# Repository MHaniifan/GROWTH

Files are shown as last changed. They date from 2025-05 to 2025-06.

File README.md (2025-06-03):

## GROWTH: Greenhouse Remote Operations With Temperature & Humidity

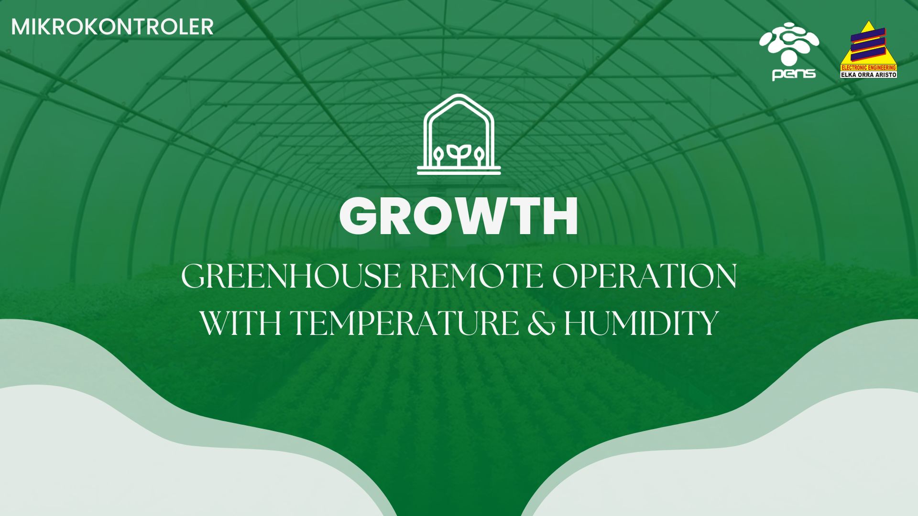
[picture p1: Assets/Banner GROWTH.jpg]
Logo GROWTH


<div align="justify">
    Proyek ini bertujuan untuk mengembangkan sistem automasi cerdas berbasis Mikrokontroler AVR untuk Smart Farming, menggunakan komponen utama seperti Arduino Mega, sensor YL-69 dan DHT-11, serta pompa air dan kipas. Arduino Mega bertindak sebagai mikrokontroler utama yang mengontrol komunikasi antar sensor dan aktuator, memungkinkan pemantauan dan pengontrolan secara real-time. Sistem ini menggunakan Timer pada AVR untuk menjaga sinkronisasi waktu, dan Interrupt untuk menyalakan Pompa Air ketika kelembaban dibawah batas.
</div>

<div align="justify">
    Pompa Air akan menyala setiap jadwal penyiraman yang sudah ditentukan. Dimana jadwal penyiraman dan lama pompa menyala, diatur pada GUI pada Komputer yang terhubung ke Mikrokontroler menggunakan komunikasi UART. Untuk Kipas akan menyala setiap suhu telah melewati batas yang ditentukan, dimana batas suhunya dapat diatur pada GUI.
</div>

<div align="justify">
    Dengan menggunakan UART, seluruh data dari sensor-sensor ini dikirimkan ke Komputer. Memungkinkan petani untuk memantau penggunaan energi dan kondisi lingkungan secara langsung dari Komputer. Sistem ini dirancang untuk meningkatkan efisiensi energi, hasil produksi, serta dapat mengurangi kerugian dengan mengotomatiskan berbagai fungsi dan memberikan kendali yang lebih fleksibel.
</div>

## Supported By :
>- Dosen Pengampu : Akhmad Hendriawan ST., MT. (NIP.197501272002121003)
>- Mata kuliah : Mikrokontroler
>- Program Studi : Sarjana Terapan Teknik Elektronika
>- Politeknik Elektronika Negeri Surabaya<br> 

## Team Member :
| NRP | Nama | Jobdesk | Github |
| :---:|:---:| :---:| :-----:|
| 2123600007 | Muhammad Haniifan  | Project Manager | [Haniifan](https://github.com/MHaniifan)
| 2123600011 | Monalisa Br. Sidauruk | Hardware Specialist | [Lisa](https://github.com/MonalisaSidauruk)
| 2123600015 | Fakhrihans Ardiyanto | UI/UX Designer | [Rihan](https://github.com/FakhrihansArdiyanto)
| 2123600027 | Darda Drestanala | 3D Designer | [Darda](https://github.com/dardadrestanala)
| 2123600029 | Aurora Putri Salsabillah Rofii | PCB Designer | [Aurora](https://github.com/aurorapsr)
| 2124640016 | Arif Ramadhan | Programmer |[Arif](https://github.com/arif-rmdhn)

##
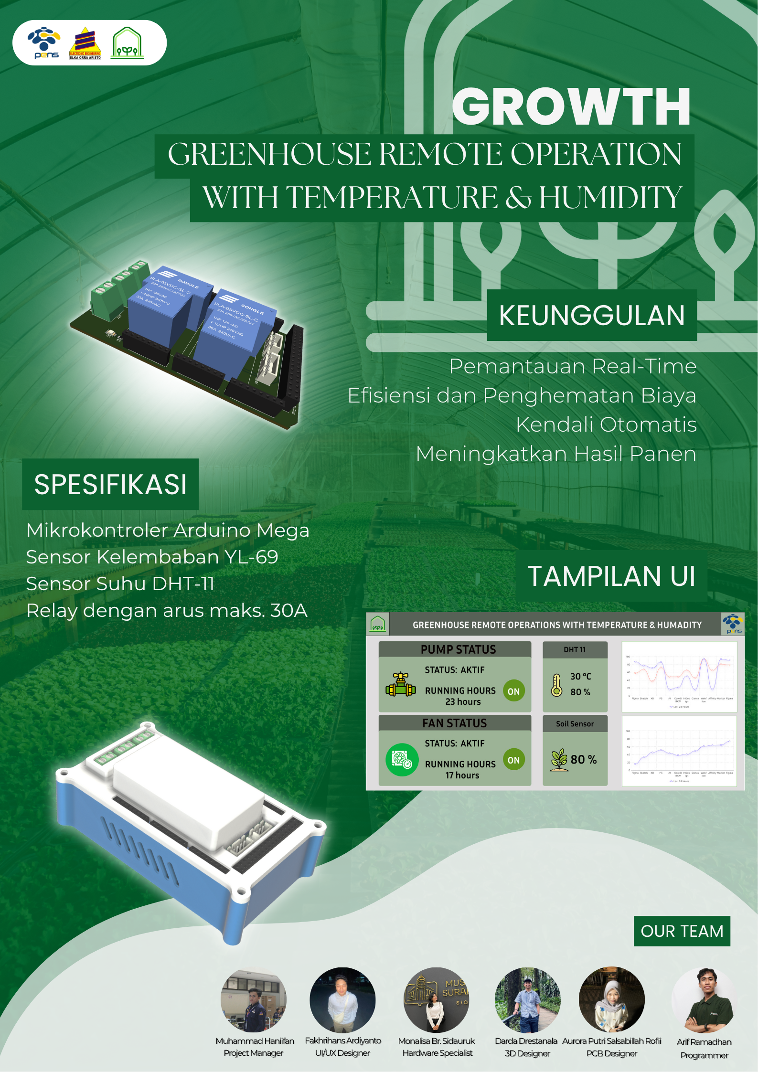
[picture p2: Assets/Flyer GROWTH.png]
Flyer GROWTH


## Daftar Isi
- [Deskripsi Project](https://github.com/MHaniifan/GROWTH#growth-greenhouse-remote-operations-with-temperaturehumidity)
- [Team Member](https://github.com/MHaniifan/GROWTH#team-member-)
- [Keunggulan](https://github.com/MHaniifan/GROWTH#keunggulan)
- [Desain Hardware](https://github.com/MHaniifan/GROWTH#desain-hardware)
- [Printed Circuit Board](https://github.com/MHaniifan/GROWTH#printed-circuit-board-pcb)
- [Program](https://github.com/MHaniifan/GROWTH#program)
- [Tampilan UI/UX](https://github.com/MHaniifan/GROWTH#tampilan-uiux)

## Keunggulan
- **Pemantauan Real-Time**: Mengukur perubahan kelembaban dan suhu dengan sensor secara terus - menerus.
- **Efisiensi dan Penghematan Biaya**: Mengurangi penggunaan listrik karena pompa dan kipas hanya dinyalakan ketika melewati batas normal tanaman.
- **Kendali Otomatis**: Menggunakan sensor untuk mengamati perubahan kondisi dan relay untuk mengaktifkan pompa dan kipas sehingga tidak dikontrol oleh manusia.
- **Meningkatkan Hasil Panen**: Mencegah tanaman kekeringan dan kepanasan sehingga dapat meningkatkan kondisi tanaman.

## Desain Hardware
Blok Diagram
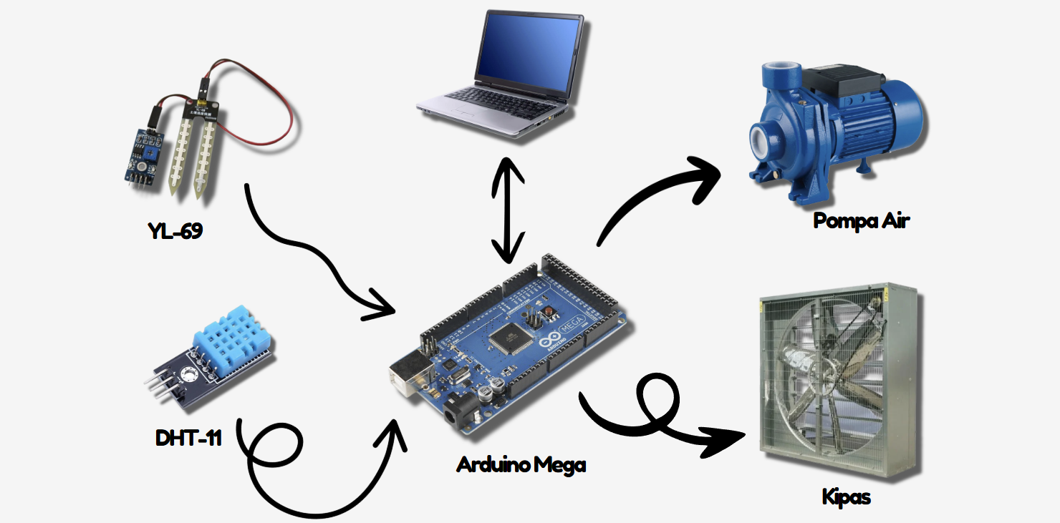
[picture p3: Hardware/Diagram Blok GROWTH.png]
Diagram Blok GROWTH


Wiring Diagram
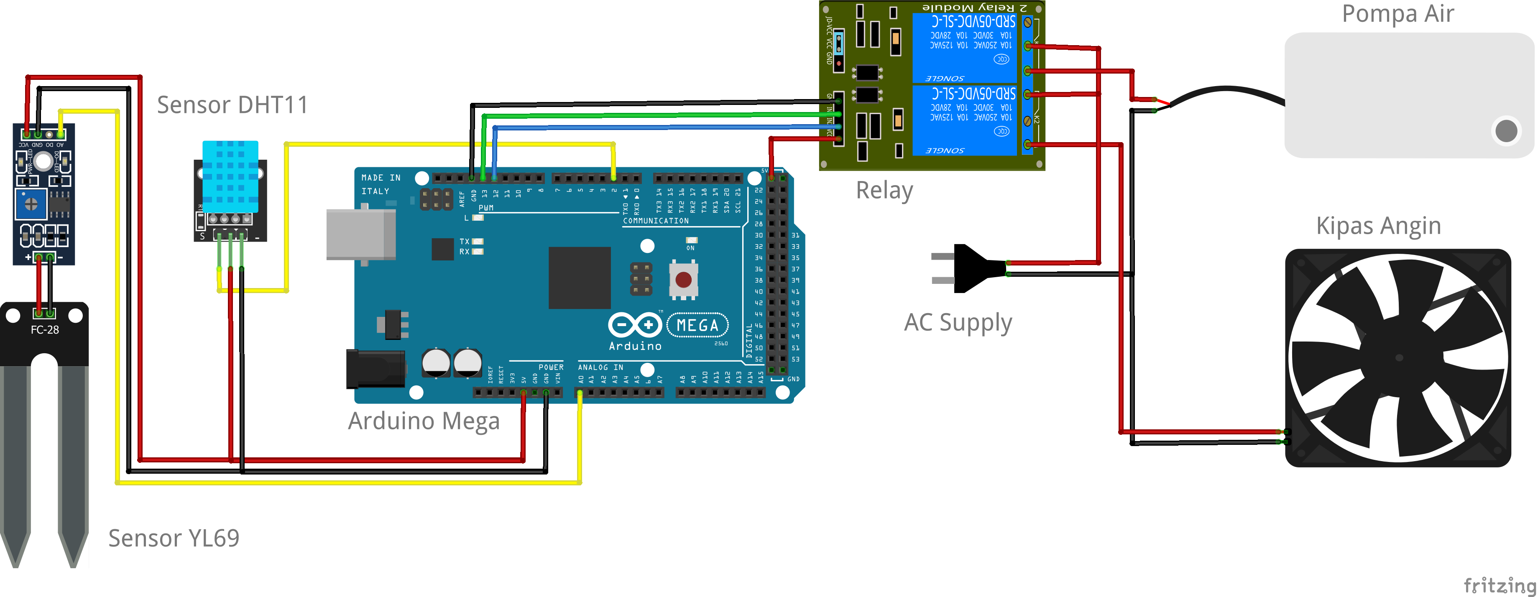
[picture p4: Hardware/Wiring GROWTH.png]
Wiring GROWTH


## Printed Circuit Board (PCB)
Skematik PCB
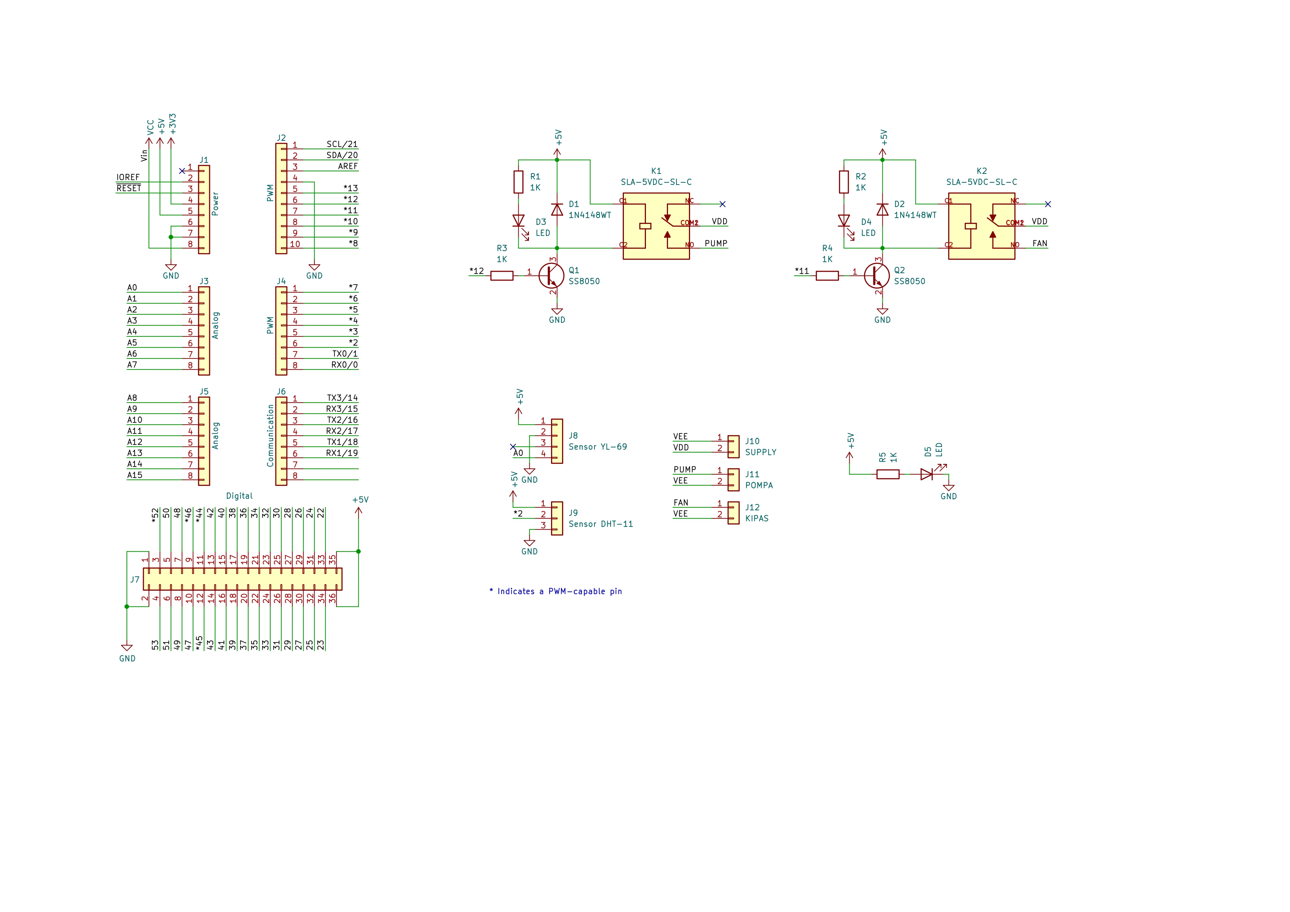
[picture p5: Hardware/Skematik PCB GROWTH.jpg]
Skematik PCB GROWTH


Desain PCB
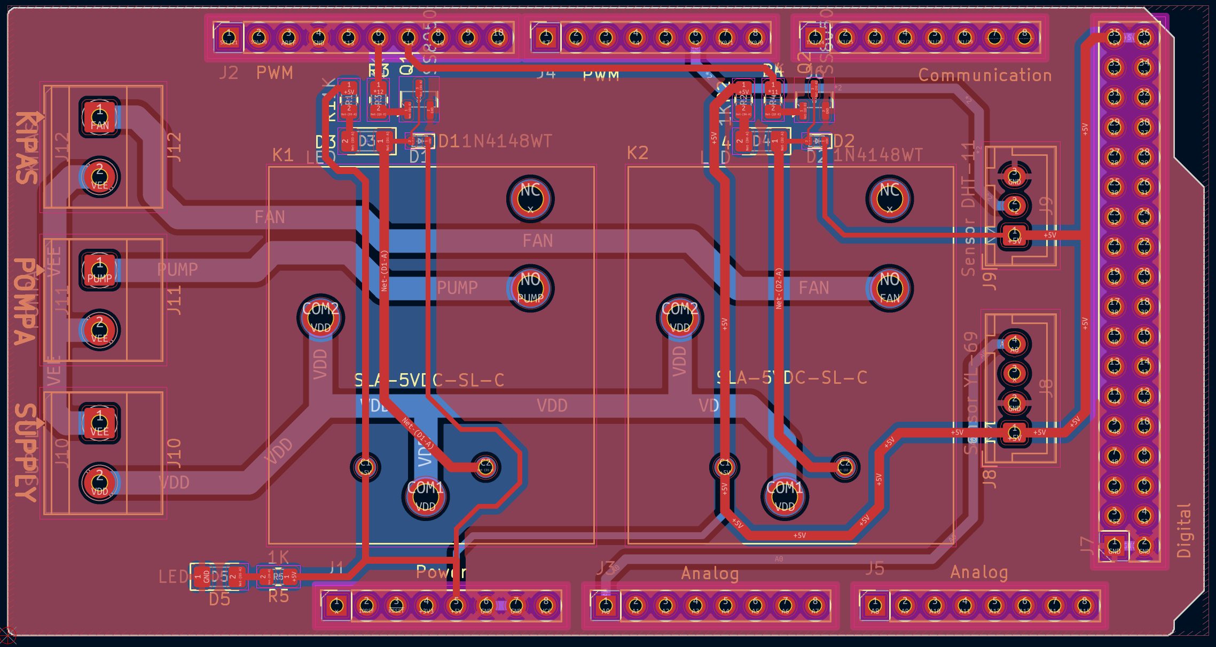
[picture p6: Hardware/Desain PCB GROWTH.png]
Desain PCB GROWTH


## Desain 3D
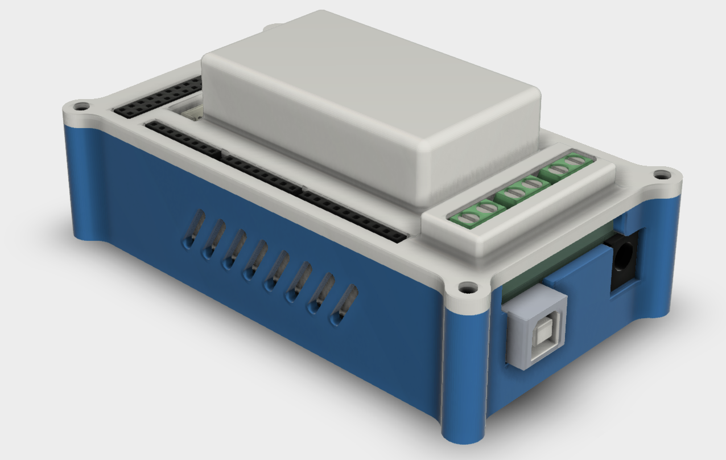
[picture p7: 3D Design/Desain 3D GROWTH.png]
Desain 3D GROWTH


## Flowchart Program
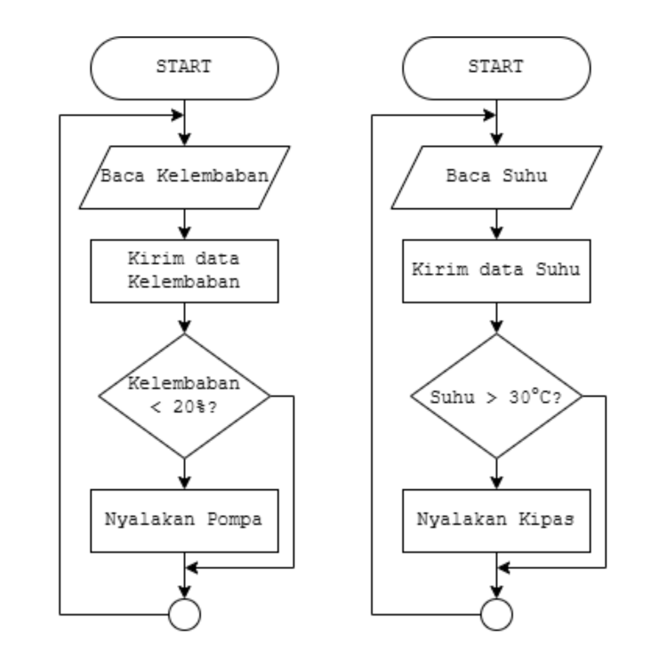
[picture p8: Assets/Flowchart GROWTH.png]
Flowchart GROWTH


## Tampilan UI/UX
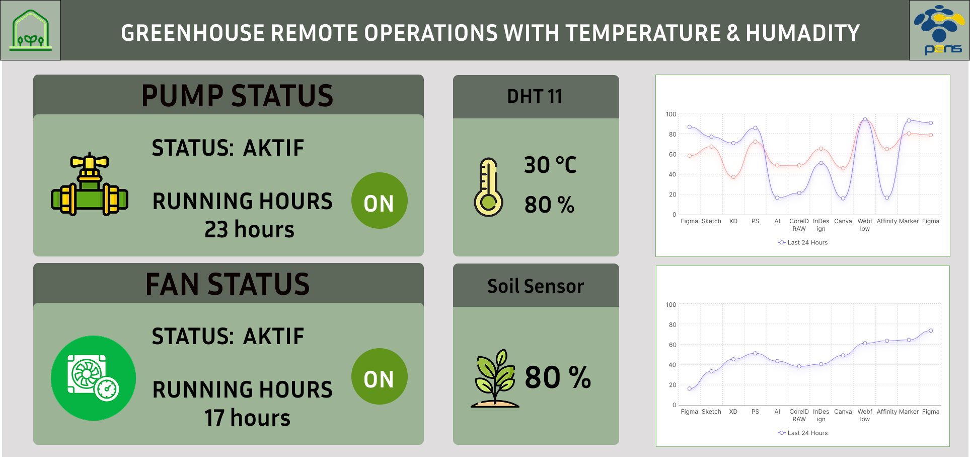
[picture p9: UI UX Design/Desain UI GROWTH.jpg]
Desain UI GROWTH


## Pengembangan Kedepannya
- Penambahan IoT untuk Pemantauan Jarak Jauh
- Penambahan RTC untuk Penjadwalan Penyiraman
- Penambahan Desain Casing yang Tahan Air
- Penambahan Baterai untuk Supply Darurat

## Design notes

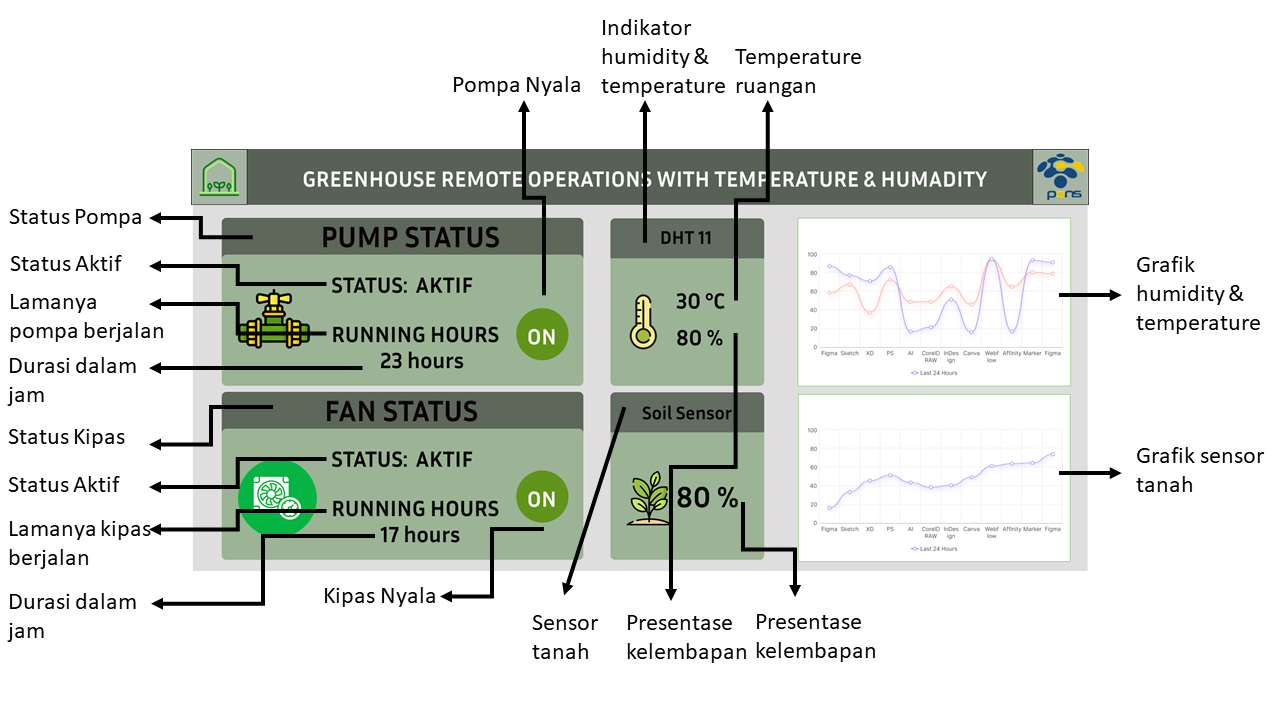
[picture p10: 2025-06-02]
UI UX Design/Deskripsi UI GROWTH.png

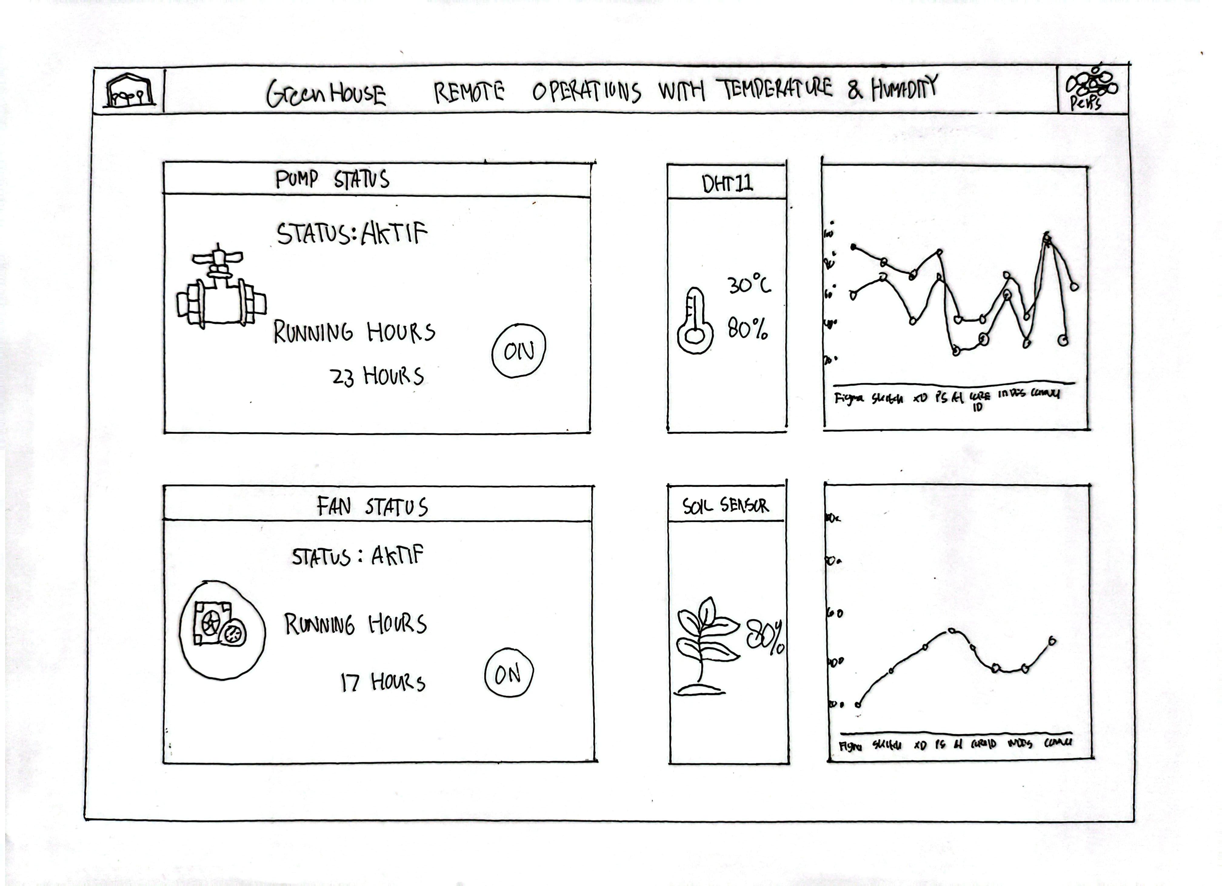
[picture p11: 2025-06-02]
UI UX Design/Sketsa UI GROWTH.jpg

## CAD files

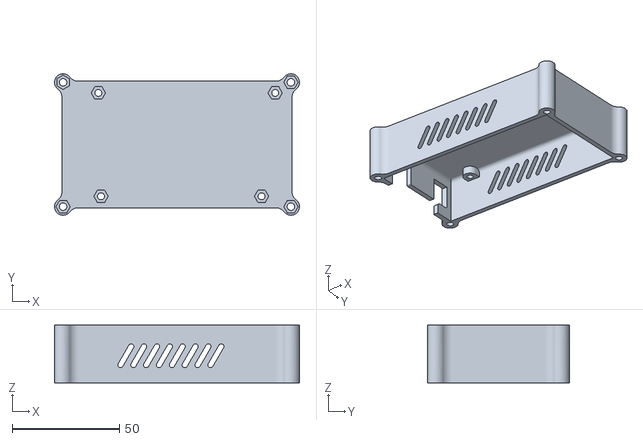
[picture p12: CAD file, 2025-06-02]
3D Design/Case_bottom-Shield.stl
114.3 x 66.0 x 27.0

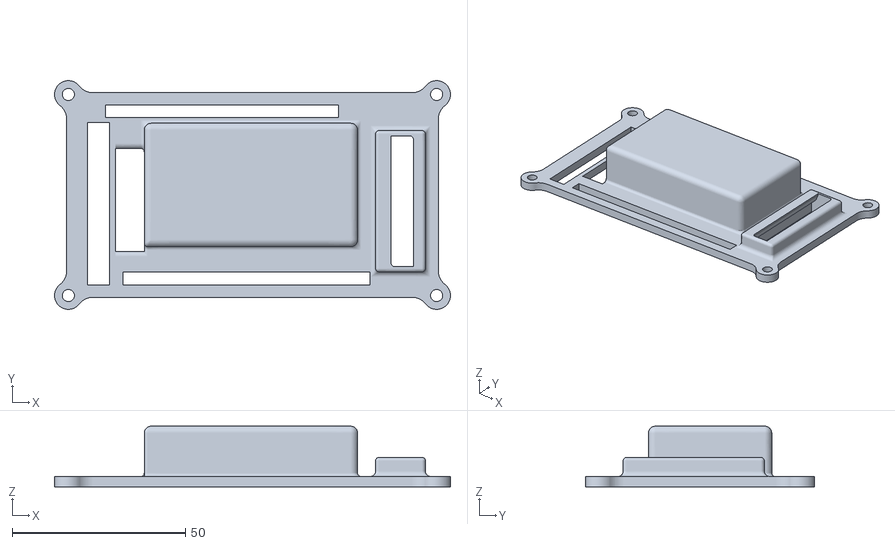
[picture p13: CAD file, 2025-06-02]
3D Design/Case_Top-Shield.stl
114.3 x 66.0 x 17.5

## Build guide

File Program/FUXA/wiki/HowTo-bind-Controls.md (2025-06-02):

To bind a **Output** Control to the Device Tag (Variable): going in editor and select the View.
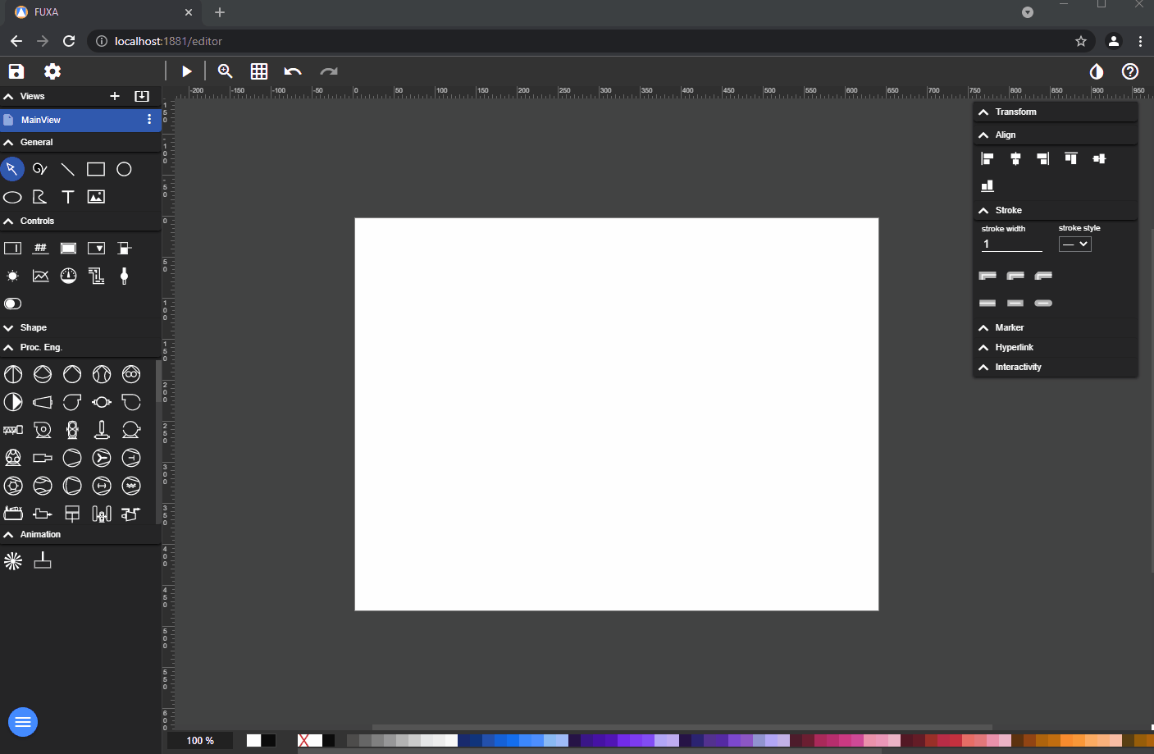
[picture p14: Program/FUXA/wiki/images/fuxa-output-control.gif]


To bind a **Input** Control to Device Tag.
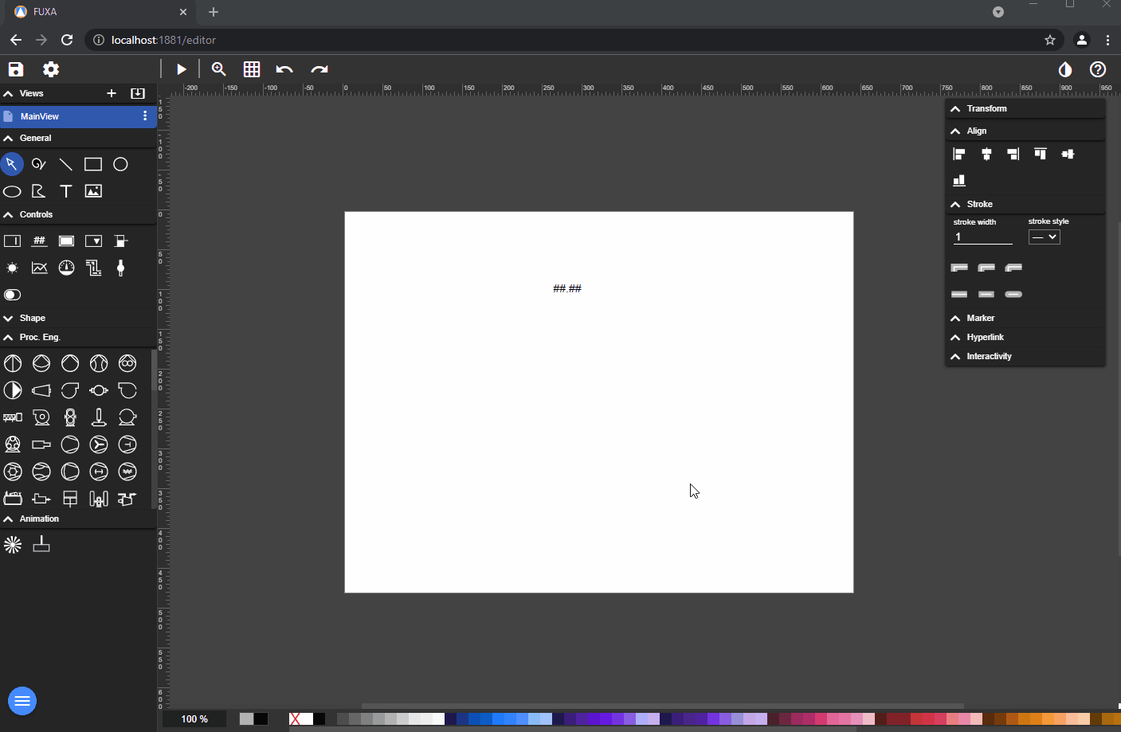
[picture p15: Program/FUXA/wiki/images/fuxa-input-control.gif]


To bind a **Select** Control to Device Tag.
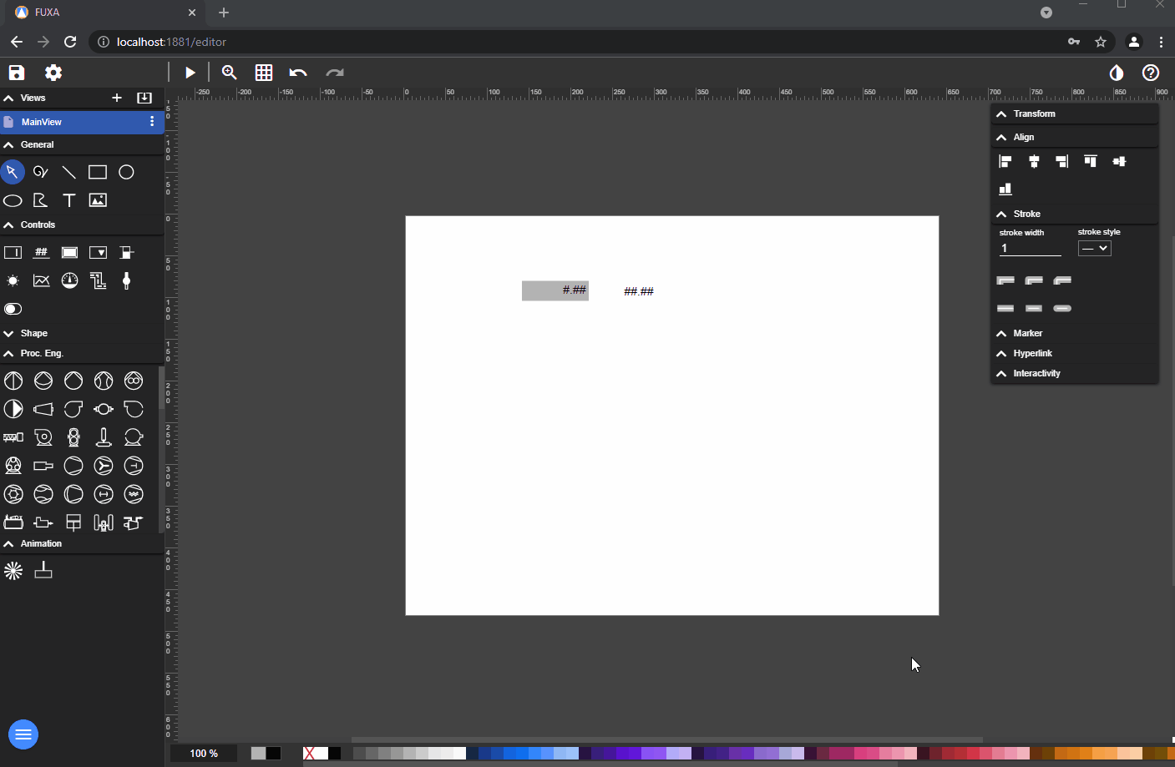
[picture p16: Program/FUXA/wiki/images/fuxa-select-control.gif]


To bind a **Slider** Control to Device Tag.
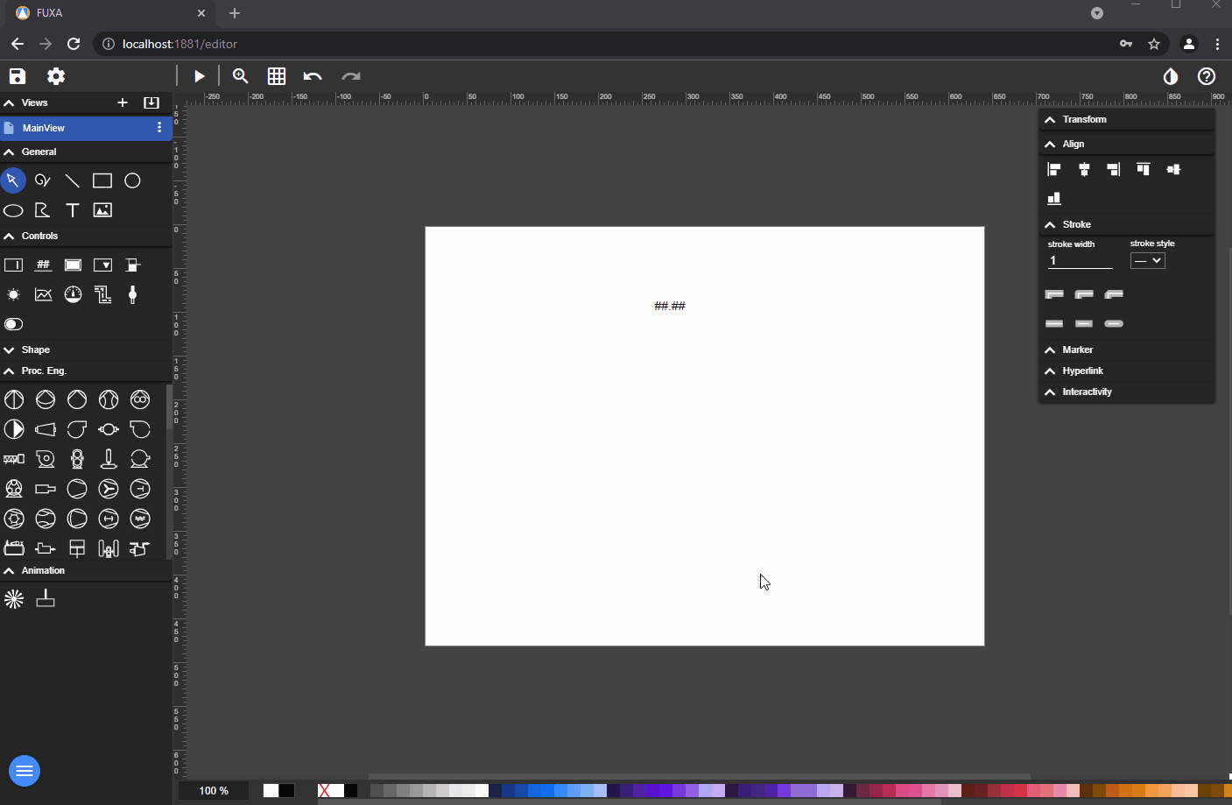
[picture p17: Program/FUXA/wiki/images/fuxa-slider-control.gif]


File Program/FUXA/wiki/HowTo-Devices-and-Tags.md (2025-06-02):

To add your Device and Tags going to **Connections** in editor.

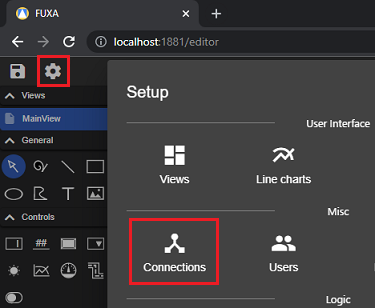
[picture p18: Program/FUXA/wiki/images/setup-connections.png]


Add and connect a **OPCUA** device.
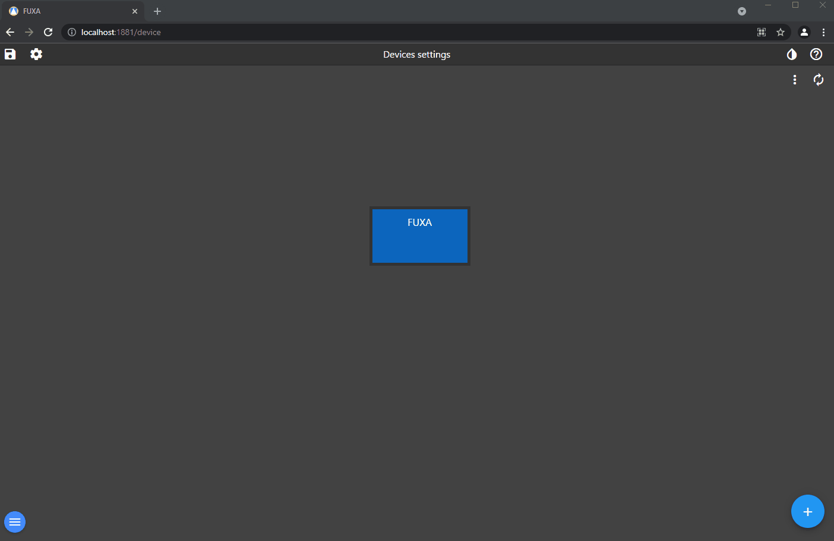
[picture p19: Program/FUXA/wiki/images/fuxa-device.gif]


To add OPCUA Tags the device have to be connected.
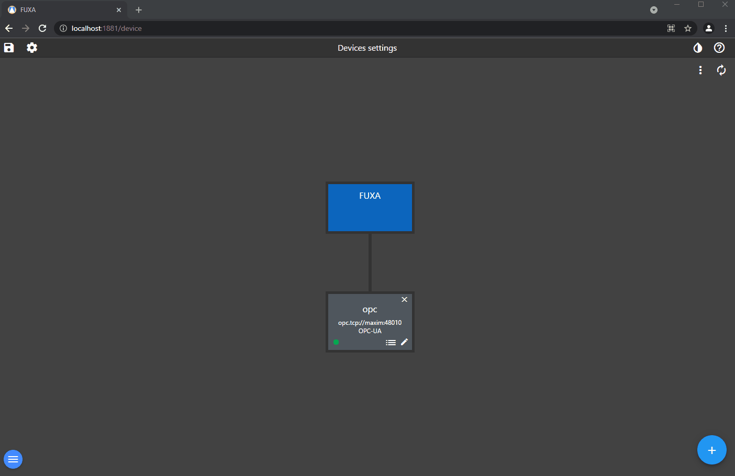
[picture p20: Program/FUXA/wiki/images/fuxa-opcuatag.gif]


To add a **Modbus** connection you have to install the driver in **Plugins**


Add a **MQTT** connection and a topic subscription
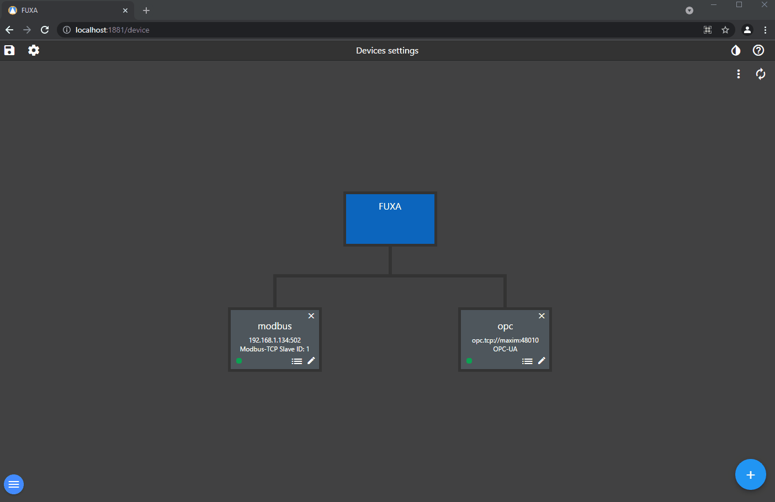
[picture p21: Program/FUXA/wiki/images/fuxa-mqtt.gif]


Add a **WebAPI** connection and a Tag of the JSON result
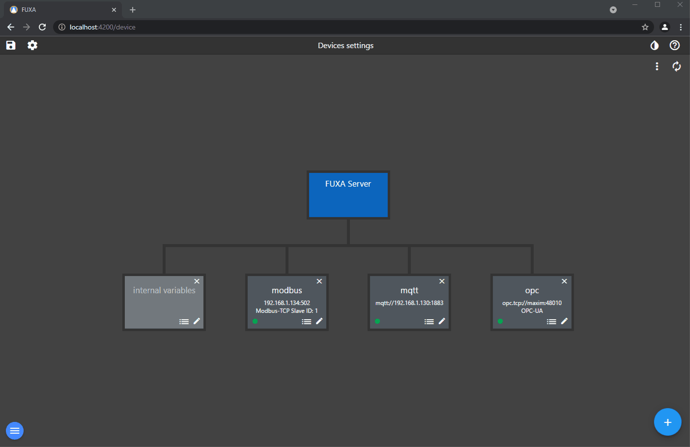
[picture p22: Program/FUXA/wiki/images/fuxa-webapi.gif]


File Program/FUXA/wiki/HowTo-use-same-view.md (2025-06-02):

You can reuse the same **View** for repeating components like pumps and valves.

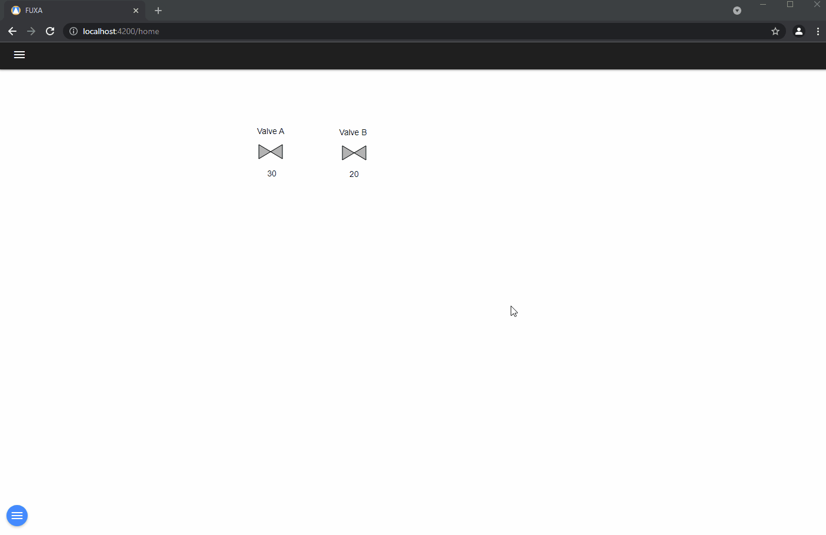
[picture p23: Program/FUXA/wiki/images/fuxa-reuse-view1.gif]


You have to define a device as **internal** and some variable (Tag) and bind it to the controls of reusable **View**.
For example the title dialog and a variable for the input value.

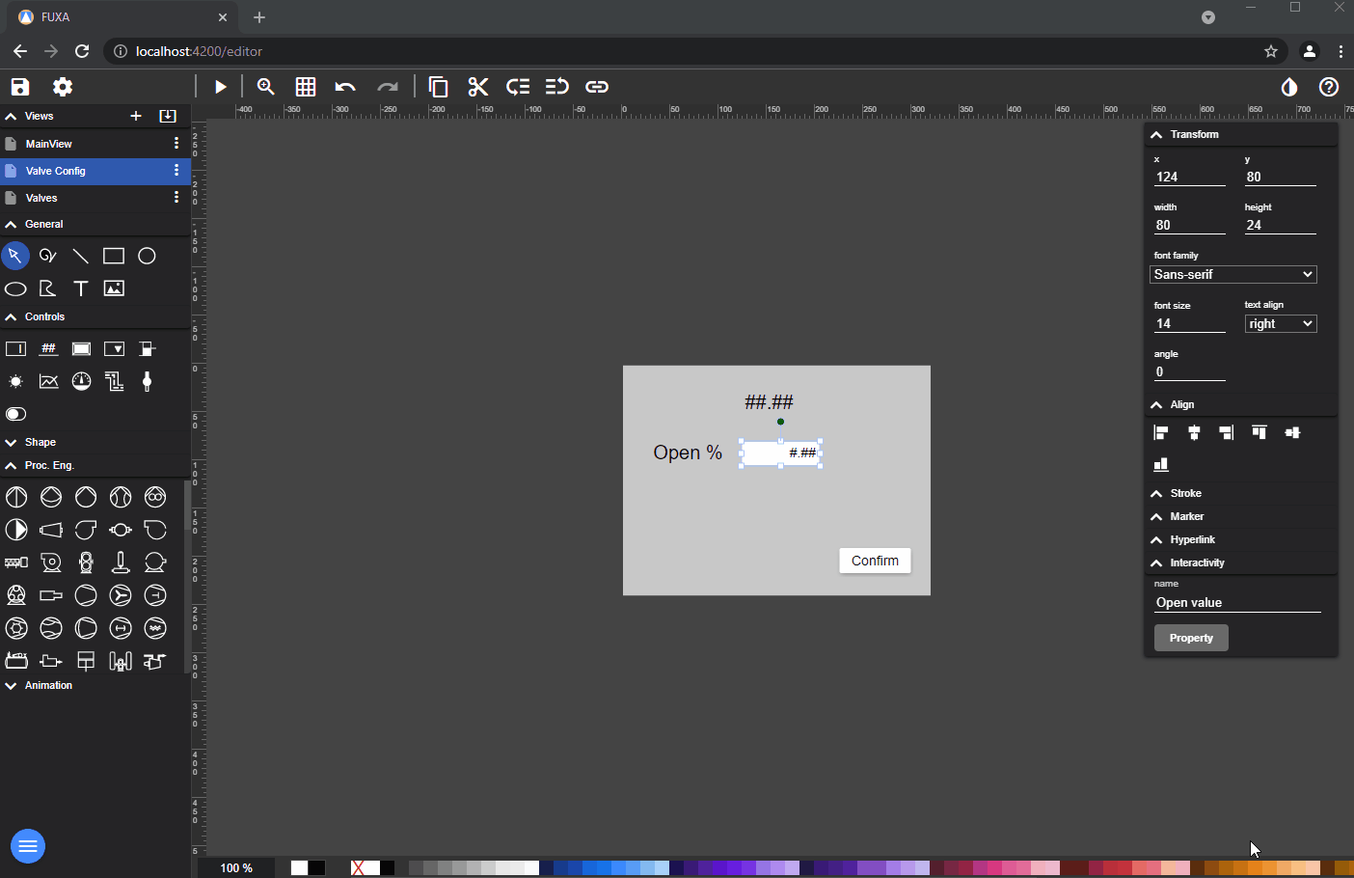
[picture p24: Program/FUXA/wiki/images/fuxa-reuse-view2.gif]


Than you define in every components the **Events** to open the dialog, where you define the connections of the internal tags with those of the device.

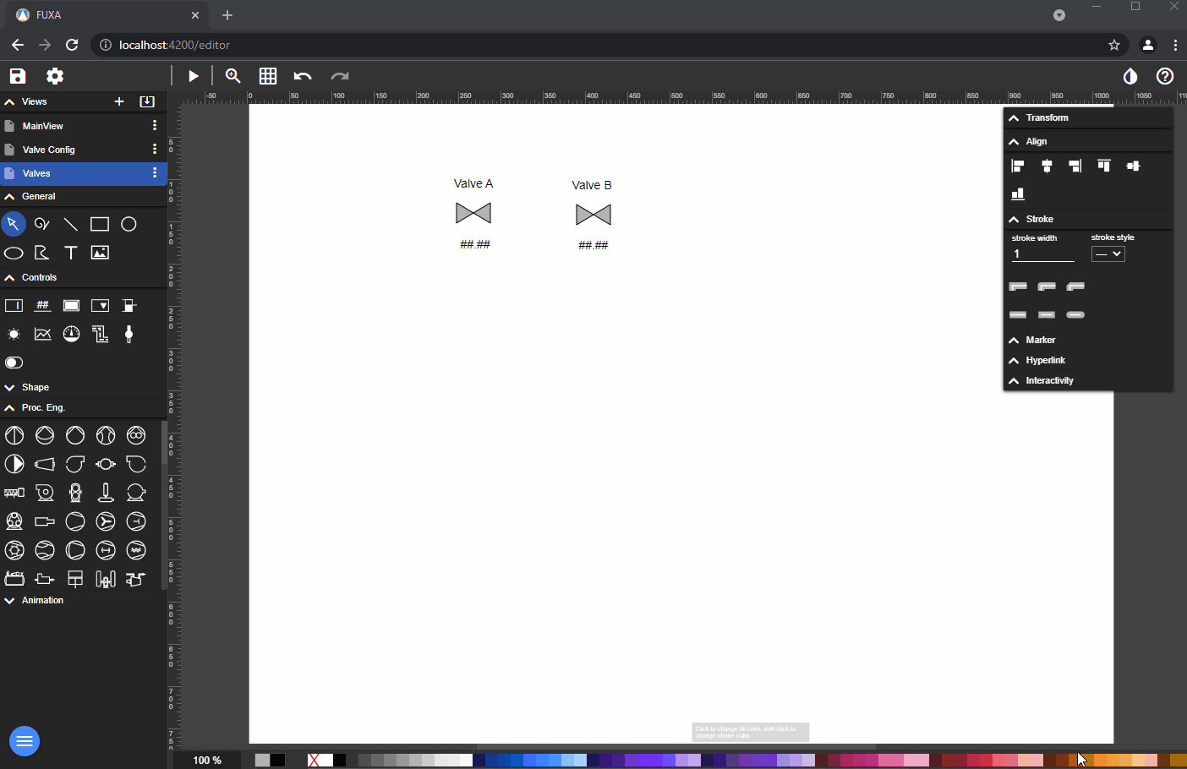
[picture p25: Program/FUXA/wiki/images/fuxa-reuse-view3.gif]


If you wish, you can also add a confirmation button.

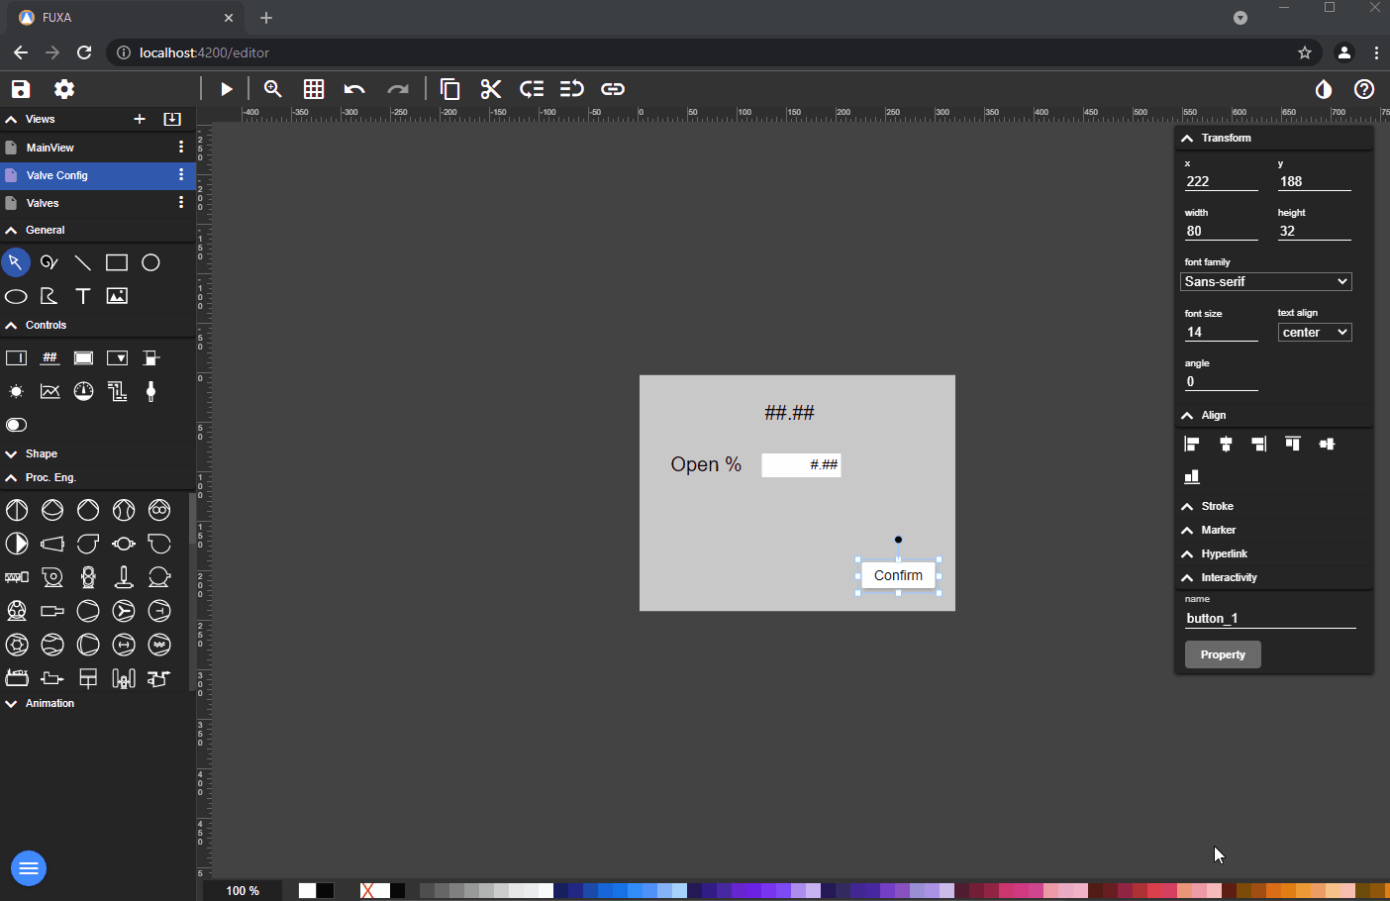
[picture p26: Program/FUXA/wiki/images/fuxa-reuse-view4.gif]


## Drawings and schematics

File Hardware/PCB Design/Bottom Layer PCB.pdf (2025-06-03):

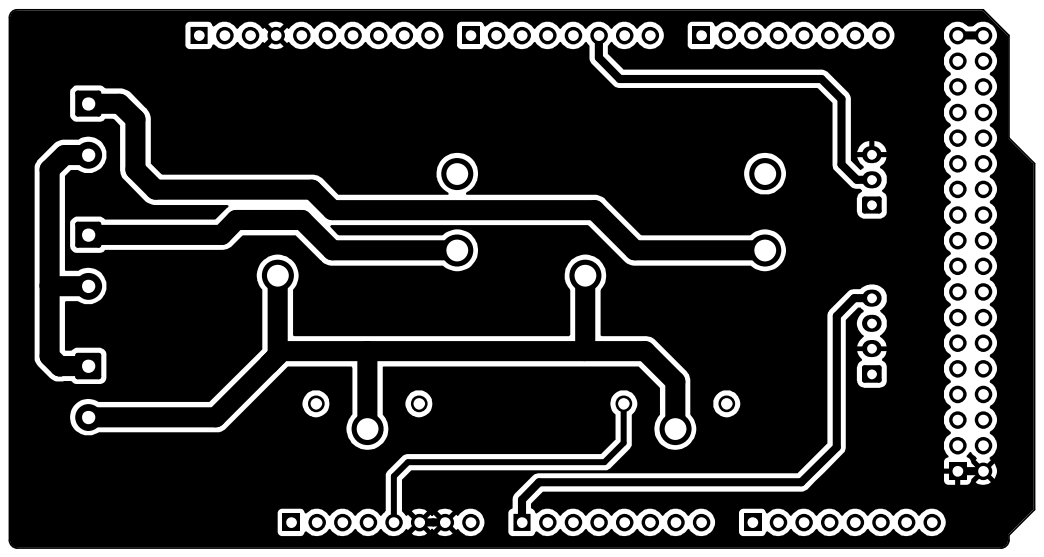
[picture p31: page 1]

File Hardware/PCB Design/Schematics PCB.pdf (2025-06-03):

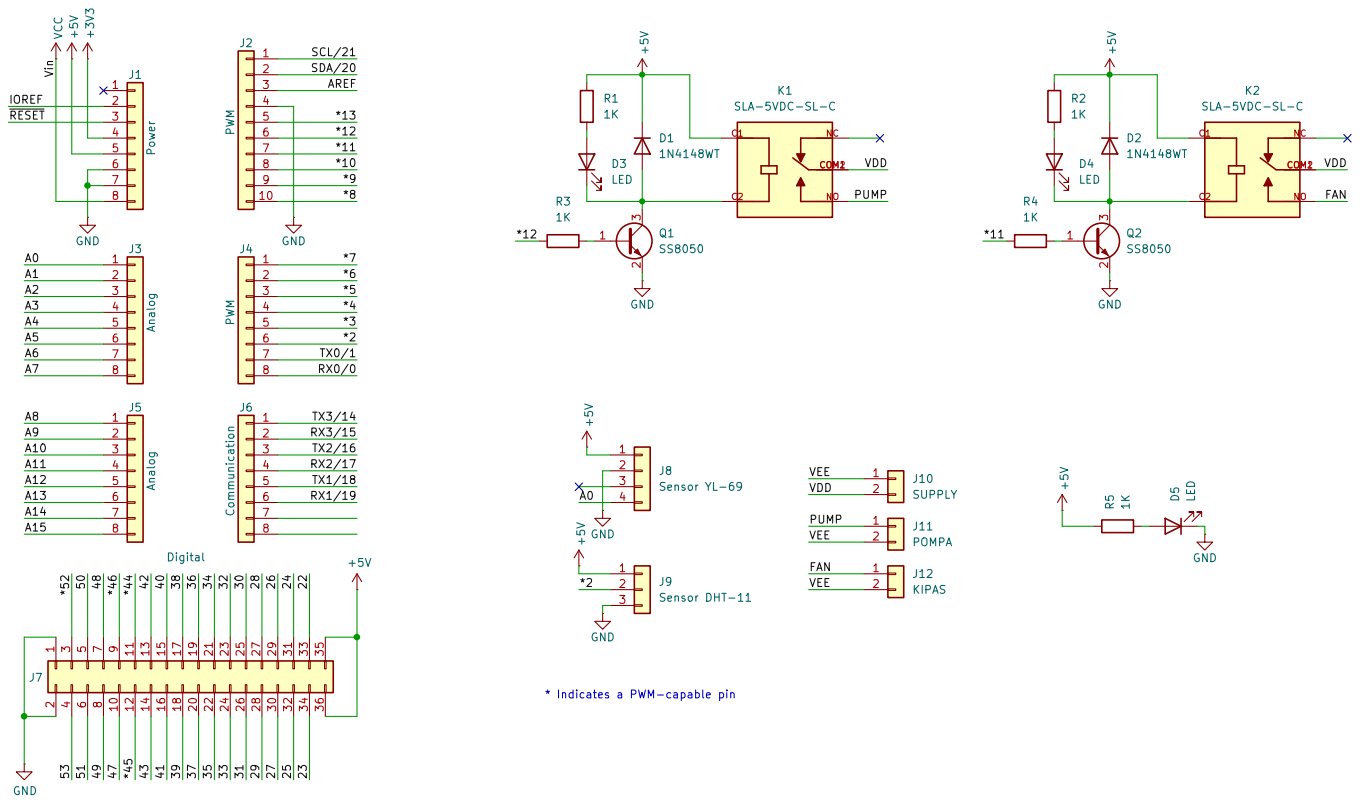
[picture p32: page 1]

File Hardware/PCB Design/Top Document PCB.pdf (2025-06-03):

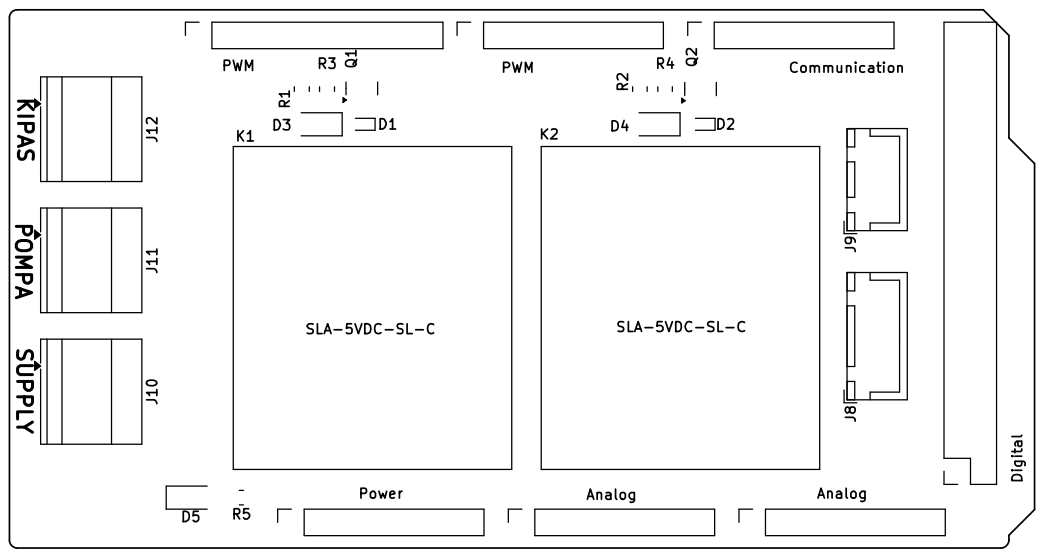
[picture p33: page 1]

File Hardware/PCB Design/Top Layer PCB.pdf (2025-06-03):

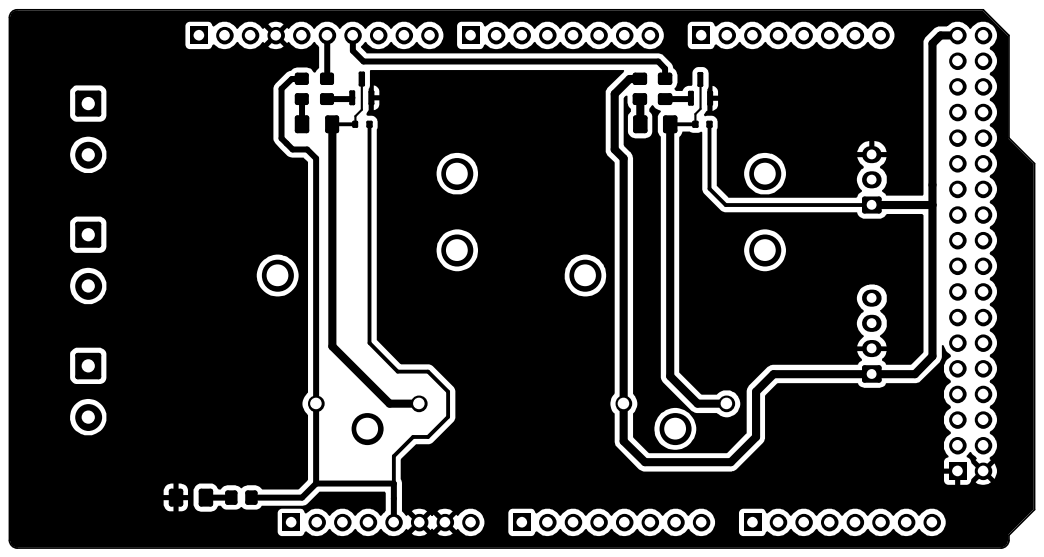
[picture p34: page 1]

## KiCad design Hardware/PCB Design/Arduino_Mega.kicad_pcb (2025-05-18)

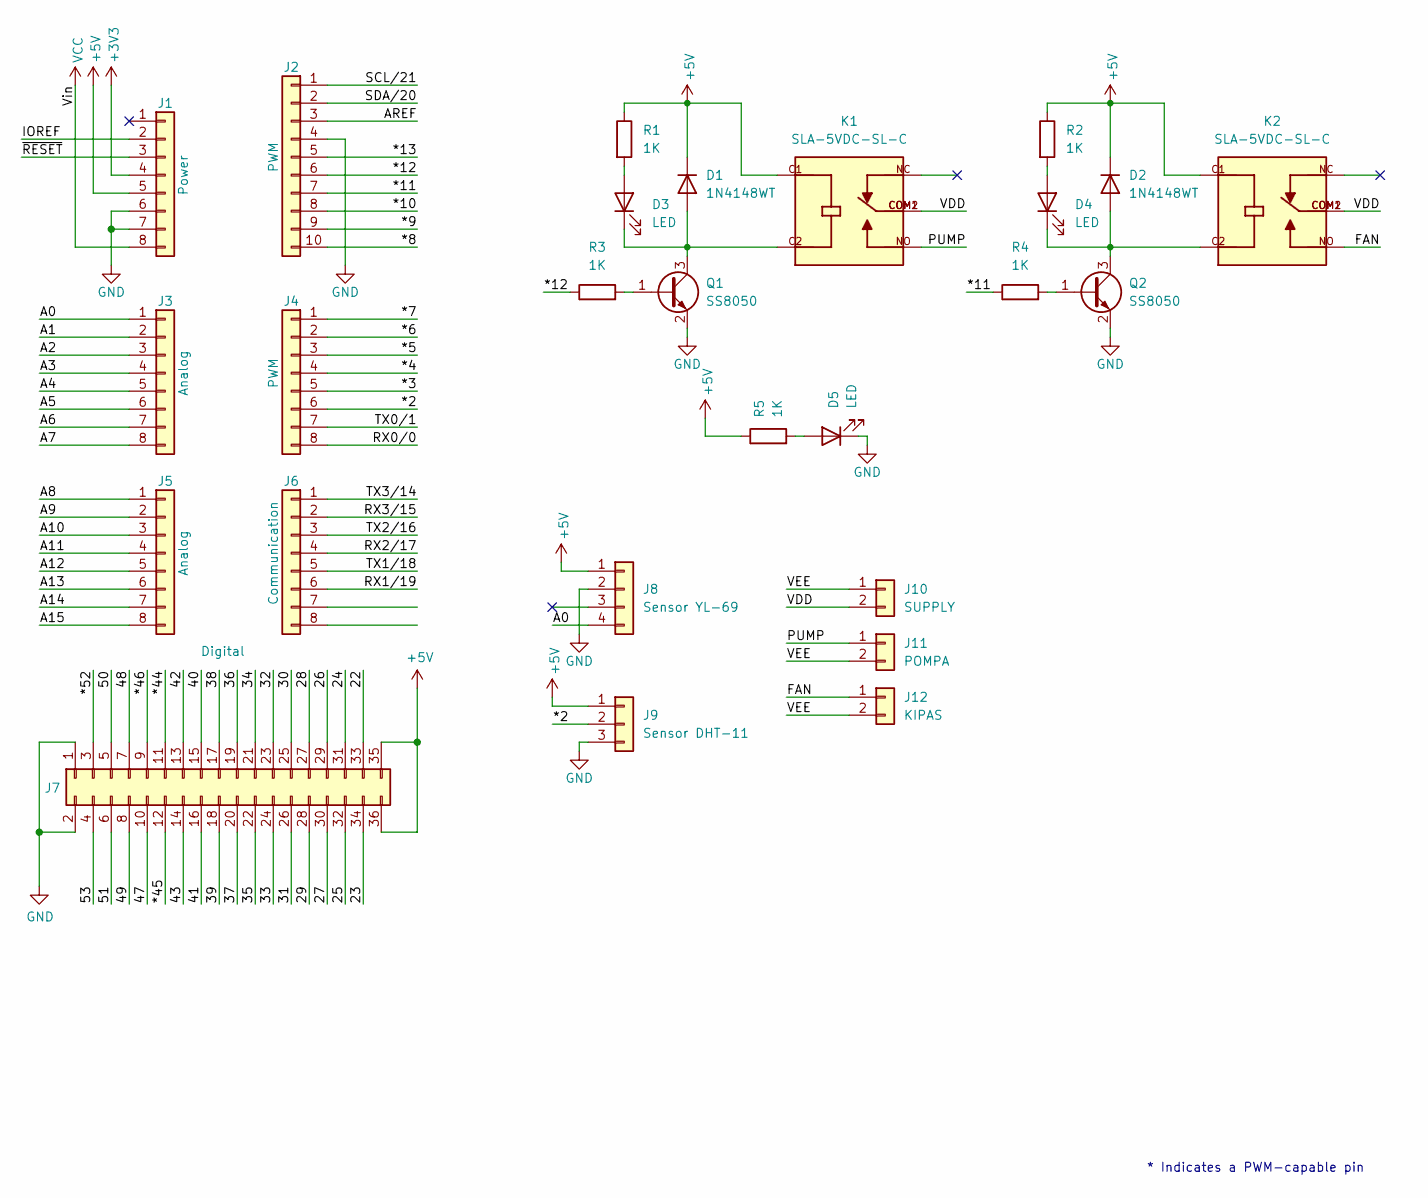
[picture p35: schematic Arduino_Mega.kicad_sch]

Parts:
D1, D2: 1N4148WT; D_SOD-523
D3, D4, D5: LED; LED_1206_3216Metric_Pad1.42x1.75mm_HandSolder
J1: Power; PinSocket_1x08_P2.54mm_Vertical
J2: PWM; PinSocket_1x10_P2.54mm_Vertical
J3, J5: Analog; PinSocket_1x08_P2.54mm_Vertical
J4: PWM; PinSocket_1x08_P2.54mm_Vertical
J6: Communication; PinSocket_1x08_P2.54mm_Vertical
J7: Digital; PinSocket_2x18_P2.54mm_Vertical
J8: Sensor YL-69; JST_XH_B4B-XH-A_1x04_P2.50mm_Vertical
J9: Sensor DHT-11; JST_XH_B3B-XH-A_1x03_P2.50mm_Vertical
J10: SUPPLY; TerminalBlock_Phoenix_MKDS-1,5-2-5.08_1x02_P5.08mm_Horizont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
J11: POMPA; TerminalBlock_Phoenix_MKDS-1,5-2-5.08_1x02_P5.08mm_Horizont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
J12: KIPAS; TerminalBlock_Phoenix_MKDS-1,5-2-5.08_1x02_P5.08mm_Horizont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
K1, K2: SLA-5VDC-SL-C; RELAY_SLA-12VDC-SL-C
Q1, Q2: SS8050; SOT-23
R1, R2, R3, R4, R5: 1K; R_0805_2012Metric_Pad1.20x1.40mm_HandSolder

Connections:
+3V3: J1.4
+5V: D1.1 (K), D2.1 (K), J1.5, J7.35, J7.36, J8.1, J9.1, K1.C1, K2.C1, R1.1, R2.1, R5.1
/22: J7.33
/23: J7.34
/24: J7.31
/25: J7.32
/26: J7.29
/27: J7.30
/28: J7.27
/29: J7.28
/30: J7.25
/31: J7.26
/32: J7.23
/33: J7.24
/34: J7.21
/35: J7.22
/36: J7.19
/37: J7.20
/38: J7.17
/39: J7.18
/40: J7.15
/41: J7.16
/42: J7.13
/43: J7.14
/47: J7.10
/48: J7.7
/49: J7.8
/50: J7.5
/51: J7.6
/53: J7.4
/*2: J4.6, J9.2
/*3: J4.5
/*4: J4.4
/*5: J4.3
/*6: J4.2
/*7: J4.1
/*8: J2.10
/*9: J2.9
/*10: J2.8
/*11: J2.7, R4.1
/*12: J2.6, R3.1
/*13: J2.5
/*44: J7.11
/*45: J7.12
/*46: J7.9
/*52: J7.3
/A0: J3.1, J8.4
/A1: J3.2
/A2: J3.3
/A3: J3.4
/A4: J3.5
/A5: J3.6
/A6: J3.7
/A7: J3.8
/A8: J5.1
/A9: J5.2
/A10: J5.3
/A11: J5.4
/A12: J5.5
/A13: J5.6
/A14: J5.7
/A15: J5.8
/AREF: J2.3
/FAN: J12.1, K2.NO
/IOREF: J1.2
/PUMP: J11.1, K1.NO
/RX0/0: J4.8
/RX1/19: J6.6
/RX2/17: J6.4
/RX3/15: J6.2
/SCL/21: J2.1
/SDA/20: J2.2
/TX0/1: J4.7
/TX1/18: J6.5
/TX2/16: J6.3
/TX3/14: J6.1
/VDD: J10.2, K1.COM1, K1.COM2, K2.COM1, K2.COM2
/VEE: J10.1, J11.2, J12.2
/~RESET: J1.3
GND: D5.1 (K), J1.6, J1.7, J2.4, J7.1, J7.2, J8.2, J9.3, Q1.2 (E), Q2.2 (E)
unnamed: D1.2 (A), D3.1 (K), K1.C2, Q1.3 (C)
unnamed: D2.2 (A), D4.1 (K), K2.C2, Q2.3 (C)
unnamed: D3.2 (A), R1.2
unnamed: D4.2 (A), R2.2
unnamed: D5.2 (A), R5.2
unnamed: Q1.1 (B), R3.2
unnamed: Q2.1 (B), R4.2
VCC: J1.8

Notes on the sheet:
* Indicates a PWM-capable pin

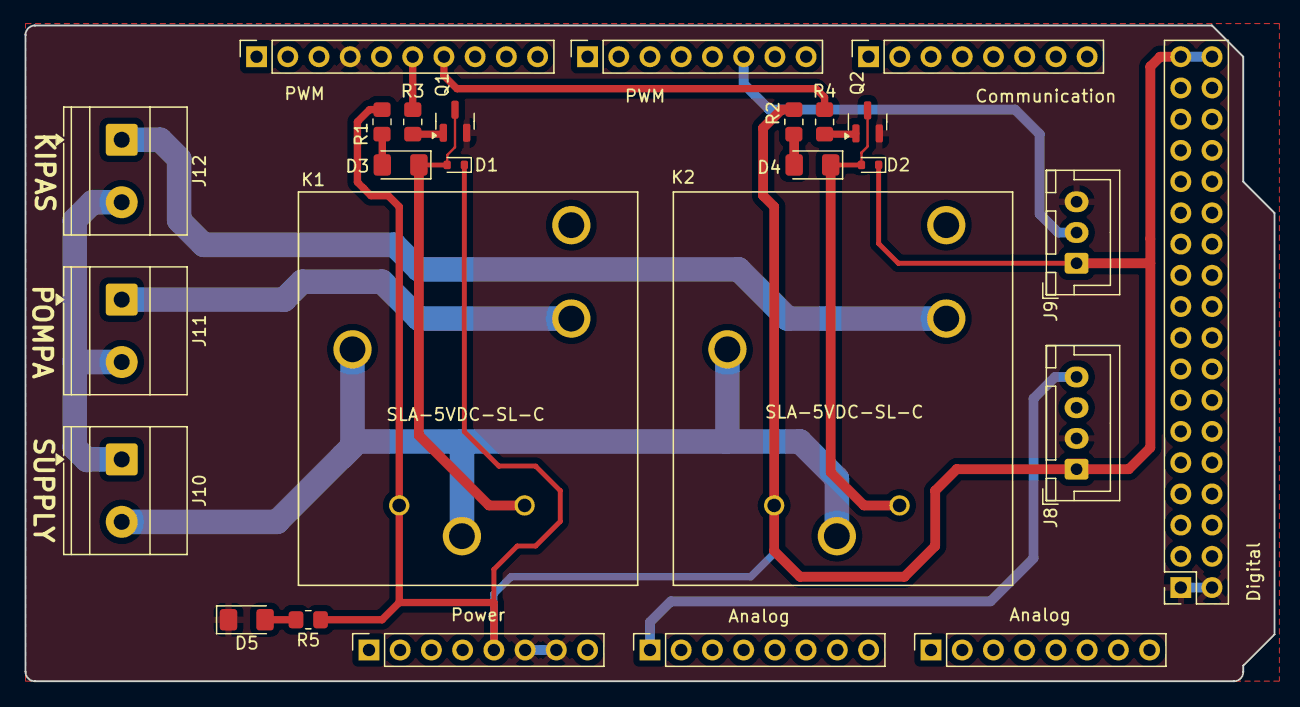
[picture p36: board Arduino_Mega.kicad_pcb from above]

Board: 2 copper layers, 101.6 x 53.3 mm, 26 parts (0 on the bottom side), 17 nets.

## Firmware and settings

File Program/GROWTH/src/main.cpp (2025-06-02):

#include <avr/io.h>
#include <util/delay.h>
#include <stdint.h>
#include <stdio.h>
#include <stdlib.h>
#include "analog.h"
#include "uart.h"
#include "millis.h"

#define BAUDRATE 9600
#define VBAUDRATE (F_CPU / ((unsigned long)BAUDRATE * 16) - 1)
#define BAUDH VBAUDRATE / 256
#define BAUDL VBAUDRATE % 256

#define DHT_PORT PORTE
#define DHT_DDR DDRE
#define DHT_PINR PINE
#define DHT_BIT 4

// Wait for a logical level on DHT pin, return timeout flag
static uint8_t wait_level(uint8_t level, uint16_t timeout)
{
  uint16_t count = 0;
  while (((DHT_PINR >> DHT_BIT) & 1) != level)
  {
    _delay_us(1);
    if (++count > timeout)
      return 1;
  }
  return 0;
}

// Read raw bits from DHT11
uint8_t dht11_read(uint8_t *humi, uint8_t *temp)
{
  uint8_t data[5] = {0};

  // Start signal: pull low >18ms
  DHT_DDR |= (1 << DHT_BIT);   // output
  DHT_PORT &= ~(1 << DHT_BIT); // drive low
  _delay_ms(20);

  // Release and switch to input
  DHT_DDR &= ~(1 << DHT_BIT);  // input
  DHT_PORT &= ~(1 << DHT_BIT); // disable pull-up
  _delay_us(30);

  // Sensor response: low ~80us
  if (wait_level(0, 100))
    return 1;
  // then high ~80us
  if (wait_level(1, 100))
    return 2;

  // Read 40 bits
  for (uint8_t i = 0; i < 40; i++)
  {
    // Wait for start of bit (low ~50us)
    if (wait_level(0, 100))
      return 3;
    // Wait for high and measure length
    uint16_t count = 0;
    while (((DHT_PINR >> DHT_BIT) & 1) == 0)
      ;
    while (((DHT_PINR >> DHT_BIT) & 1) == 1)
    {
      _delay_us(1);
      count++;
      if (count > 100)
        break;
    }
    // If high lasted >40us, bit is 1
    data[i / 8] <<= 1;
    if (count > 40)
      data[i / 8] |= 1;
  }

  // Checksum
  uint8_t sum = data[0] + data[1] + data[2] + data[3];
  if (sum != data[4])
    return 4;

  *humi = data[0];
  *temp = data[2];
  return 0;
}

unsigned int dataADC = 0;
float kelembaban = 0;
char str[50];
uint8_t humidity = 0, temperature = 0;
bool pump = 0, fan = 0;

int main(void)
{
  DDRB |= (1 << DDB6); // Output untuk indikator kelembaban tanah
  DDRB |= (1 << DDB5); // Output untuk indikator suhu

  UARTInit();
  ADCInit();
  millis_init(F_CPU); // Aktifkan timer millis

  stdout = fdevopen(UARTPutChar, NULL);

  uint8_t humidity = 0, temperature = 0;
  unsigned int dataADC = 0;
  float kelembaban = 0;
  char str[50];

  millis_t lastSendTime = millis_get(); // Waktu pengiriman terakhir

  while (1)
  {
    // Cek apakah sudah lewat 500ms sejak terakhir kirim
    if ((millis_t)(millis_get() - lastSendTime) >= 500)
    {
      dht11_read(&humidity, &temperature); // Baca sensor DHT11
      dataADC = ADCIN(0);                  // Baca ADC
      kelembaban = ((1023.0f - dataADC) * 100.0f) / 1023.0f;
      dtostrf(kelembaban, 4, 2, str);

      // Kirim data via UART
      // printf("ADC = %d, Kelembaban = %s%%\r\n", dataADC, str);
      printf("Kelembaban Tanah = %s, Kelembaban Udara = %d, Suhu = %d, Pump = %d, Fan = %d\r\n",str, humidity, temperature, (int)pump, (int)fan);

      // Update waktu terakhir pengiriman
      lastSendTime = millis_get();

      // Logika kontrol sederhana
      if (kelembaban <= 30)
      {
        PORTB |= (1 << PB6); // Nyalakan LED/Pompa jika kelembaban rendah
        pump = 1;
      }
      else
      {
        PORTB &= ~(1 << PB6);
        pump = 0;
      }

      if (temperature >= 31)
      {
        PORTB |= (1 << PB5); // Nyalakan kipas/pendingin jika panas
        fan = 1;
      }
      else
      {
        PORTB &= ~(1 << PB5);
        fan = 0;
      }
    }

    // Di sini bisa tambahkan tugas lain yang non-blocking
  }

  return 0;
}

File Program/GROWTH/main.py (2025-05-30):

import serial
import requests
import re
import time  # Untuk delay saat reconnect

# Konfigurasi Port Serial (COM11)
SERIAL_PORT = "COM11"  # Ganti dengan port yang sesuai (Linux: '/dev/ttyUSB0', Mac: '/dev/tty.usbmodem*')
BAUD_RATE = 9600

# URL API
API_URL = "http://192.168.159.163:3000/api/all/sendvalue"

# Inisialisasi Serial
def init_serial():
    try:
        return serial.Serial(
            port=SERIAL_PORT,
            baudrate=BAUD_RATE,
            timeout=1
        )
    except serial.SerialException as e:
        print(f"Gagal membuka port {SERIAL_PORT}: {e}")
        return None

# Fungsi untuk parsing data sensor
def parse_sensor_data(line):
    pattern = r"Kelembaban Tanah = (.+), Kelembaban Udara = (\d+), Suhu = (\d+), Pump = (\d+), Fan = (\d+)"
    match = re.match(pattern, line)
    if match:
        return {
            "soil": match.group(1),
            "humidity": int(match.group(2)),
            "temperature": int(match.group(3)),
            "pump": int(match.group(4)),
            "fan": int(match.group(5)),
        }
    return None

# Main loop
def main():
    ser = init_serial()
    if not ser:
        print("Konektivitas serial tidak tersedia.")
        return

    while True:
        try:
            # Baca data dari Serial
            if ser.in_waiting > 0:
                line = ser.readline().decode("utf-8").strip()
                print("Data mentah:", line)

                if line:  # Hanya proses jika ada data
                    sensor_data = parse_sensor_data(line)

                    if sensor_data:
                        # Kirim ke API
                        response = requests.put(
                            API_URL,
                            json={
                                "id": 1,
                                "soil_hum": float(sensor_data["soil"]),
                                "dht_hum": int(sensor_data["humidity"]),
                                "dht_temp":int(sensor_data["temperature"]),
                                "fan_stat": int(sensor_data["fan"]),
                                "pump_stat": int(sensor_data["pump"]),
                                "fan_hour": 12,
                                "pump_hour": 10,
                            },
                        )
                        print("Status API:", response.status_code)
                        print("Data terkirim:", sensor_data)
                    else:
                        print("Gagal parsing data")
            time.sleep(0.1)  # Delay kecil untuk menghindari CPU overload

        except serial.SerialException as e:
            print("Error serial:", str(e))
            ser.close()
            print("Menunggu 5 detik sebelum reconnect...")
            time.sleep(5)
            ser = init_serial()
        except Exception as e:
            print("Error umum:", str(e))
            ser.close()
            print("Menunggu 5 detik sebelum reconnect...")
            time.sleep(5)
            ser = init_serial()

if __name__ == "__main__":
    main()
